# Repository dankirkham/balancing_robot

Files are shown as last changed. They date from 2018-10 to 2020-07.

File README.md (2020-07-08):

# Balancing Robot
A balancing robot that uses a PID control loop with accelerometer feedback to drive stepper motors.

## Mark 1

### Bill of Materials

#### Purchased Parts
- 2 x NEMA 17 Stepper
- 1 x Arduino Uno  
- 2 x Adafruit TB6612 1.2A DC/Stepper Motor Driver Breakout Board
- 1 x Adafruit Triple-Axis Accelerometer - ±2/4/8g @ 14-bit - MMA8451
- 1 x Protoboard
- 1 x 3S 11.1 V 1300 mAh LiPo Battery with XT-60 Connector
- 1 x XT-60 Male Connector
- Hookup Wire
- 3M Dual Lock to hold battery

#### 3D Printed Parts
- 1 x Chassis
- 1 x Circuit Mount
- 2 x Wheels

### Lessons Learned
#### Robot Center-of-Gravity
The center of gravity of the robot is too low. It can be balanced when the motors are unpowered. The robot should have been more top-heavy so that steady-state balance is much more difficult.

#### Reliance on Accelerometer
The robot relies on an accelerometer as its sole instrument for which to measure tilt angle. There are two major issues with this.

1. The stepper motors vibrate violently enough to rattle the accelerometer. When this happens, the accelerometer sees random accelerations greater than 1g. This causes angle measurements to become unreliable. However, if a low-pass filter is applied to the measurement data, this problem seems to go away. When determining a cutoff frequency for the filter, there is a trade-off between vibration noise and the disturbance response of the robot. If the cutoff frequency is too low, the robot will not right it self quickly enough when it is bumped.

2. The angle measurement is not reliable when the robot is under a translational acceleration. If the robot accelerates forward while it is not tilted, the control loop will think its tilted and try to compensate.

A future robot should make use of a gyroscope in addition to the accelerometer. A gyroscope measures rate of change of angle, so it must be integrated over time. This results in angle measurements with more instantaneous accuracy, however the gyroscope will drift over time and must be corrected by the accelerometer.

#### Traction Issues
The robot slipped on smooth surfaces. It seemed to work best on carpet. Future designs should have wheels that provide much better traction.

#### Step Angle
The stepper motors moved 1.8° per step. This resulted in very discrete movements from the robot. The wheels could be seen moving like the second-hand on a quartz clock. A future design might make use of a microstepping driver to make wheel movement more continuous.

## Mark 2

### Bill of Materials

#### Purchased Parts
- 2 x NEMA 17 Stepper
- 1 x Arduino Uno  
- 2 x Adafruit Motor Shield V2
- 1 x Adafruit 9-DOF Accel/Mag/Gyro+Temp Breakout Board - LSM9DS1
- 1 x 3S 11.1 V 1300 mAh LiPo Battery with XT-60 Connector
- 1 x XT-60 Male Connector
- Hookup Wire
- 3M Dual Lock to hold battery
- 2 x RC car tires ([amazon](https://www.amazon.com/gp/product/B0195WYZKE/))

#### 3D Printed Parts
- 1 x Chassis
- 1 x Circuit Mount
- 2 x Wheels
- 1 x Support Bracket

### Improvements Over Mark 1

#### Taller Robot
The robot is now taller and more top heavy. The old robot could sometimes balance by itself with no motor input. This version should be much less stable and require more active control input.

#### Sensors
In addition to an accelerometer, this version uses a gyroscope. The gyroscope provides angular rate data which is integrated over time to provide positional feedback to the control loop.

The sensor has been moved to be on the same axis of rotation as the wheels. I noticed that with the previous version the robot behaved differently when tilted to one side than the other. This is likely because the sensor was not mounted above/below the center of mass. I expect the sensor to perform best when mounted both under the center of mass and on the axis of rotation.

The sensor is now has some vibration damping. This should improve the accelerometer noise that was a problem on the previous robot. I opted to use double-sided foam because it was easy. I may go down the rabbit hole and experiment with other isolation/damping methods in the future.

#### Filtering
In order to combine the accelerometer data and the gyroscope data, this robot makes use of a Kalman filter. This is a statistical filter that models the dynamics of the robot to predict its state. It then uses the measurement data to correct the prediction. By taking into account the noise of the system and the measurements, it provides a very reliable prediction of the tilt angle of the robot.

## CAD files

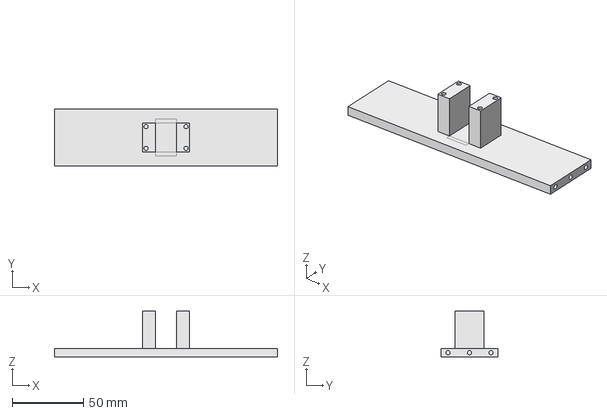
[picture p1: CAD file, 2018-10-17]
mark2/cad/sensor_bracket.FCStd
156.0 x 40.0 x 32.1 mm

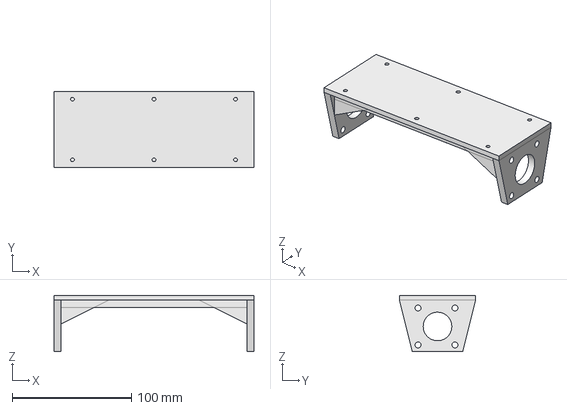
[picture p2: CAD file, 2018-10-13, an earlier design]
mark1/cad/frame.FCStd
168.0 x 64.0 x 47.3 mm

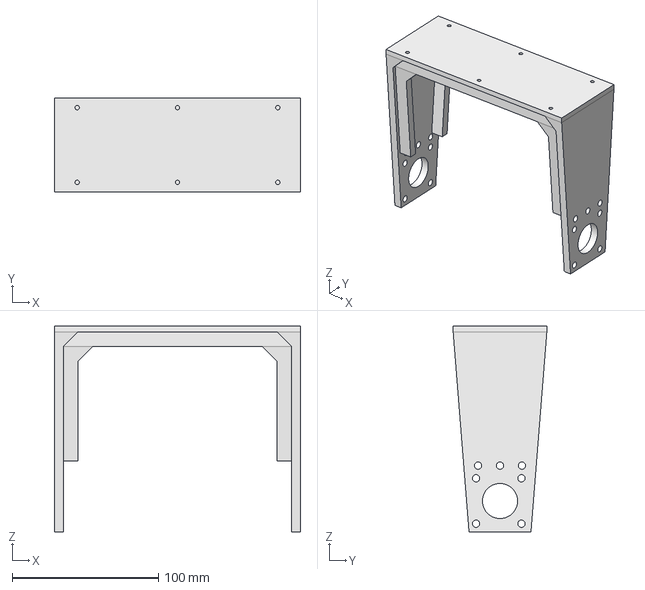
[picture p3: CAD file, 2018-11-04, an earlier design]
mark2/cad/frame.FCStd
168.0 x 64.0 x 140.7 mm

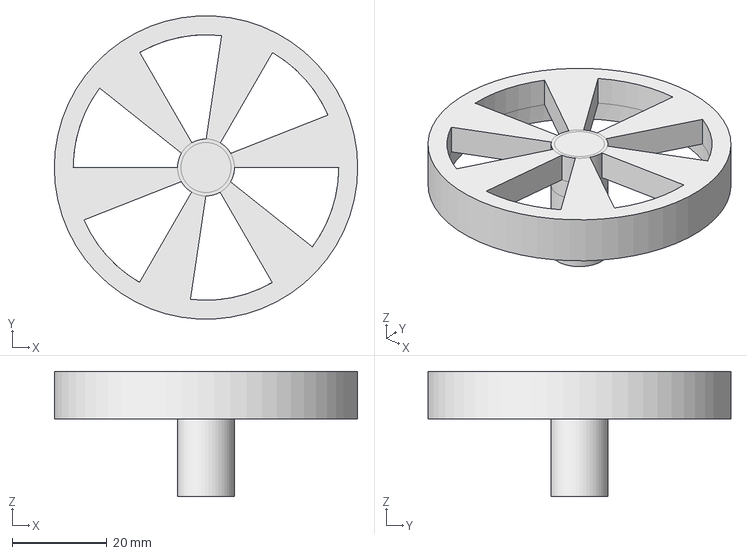
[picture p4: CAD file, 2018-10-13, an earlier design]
mark1/cad/wheel.FCStd
64.0 x 63.9 x 26.4 mm

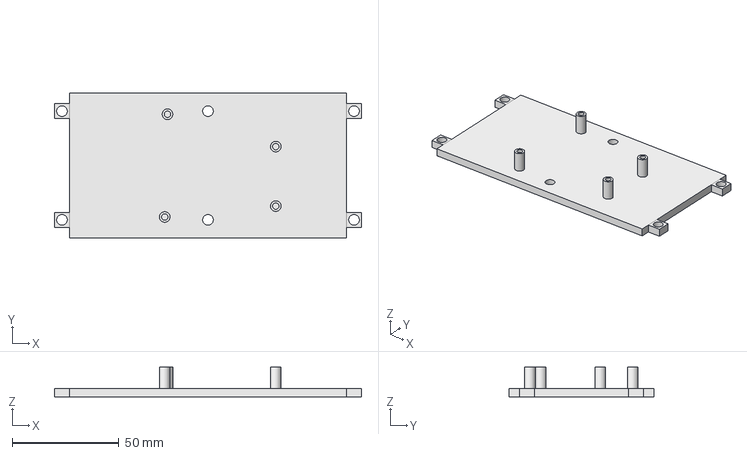
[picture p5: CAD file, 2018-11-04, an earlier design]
mark2/cad/circuit_mount.FCStd
144.0 x 68.0 x 14.0 mm

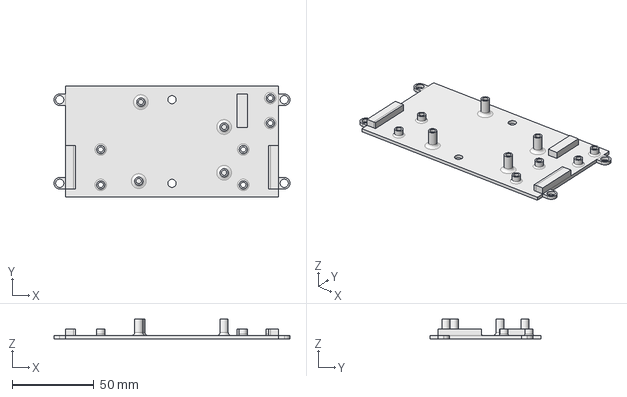
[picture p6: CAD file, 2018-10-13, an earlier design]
mark1/cad/circuit_mount.FCStd
144.0 x 68.0 x 12.0 mm

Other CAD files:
mark1/cad/circuit_mount.stl
mark1/cad/frame.stl
mark1/cad/wheel.stl
mark2/cad/circuit_mount.stl
mark2/cad/frame.stl
mark2/cad/sensor_bracket.stl

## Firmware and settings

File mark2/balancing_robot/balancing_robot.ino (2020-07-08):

#include <Adafruit_MotorShield.h>
#include <Adafruit_LSM9DS1.h>
#include <Adafruit_Sensor.h>
#include <math.h>

#define BATTERY_PIN A2
// 11 Volts
// 509 counts
// 2.494 V at ADC

// 12 Volts
// 556 Counts
// 2.721

const double P = 13;
const double I = 4;
const double D = 40;

const double FILTER_CUTOFF_HERTZ = 1;
const double FILTER_RC = 1 / (2 * M_PI * FILTER_CUTOFF_HERTZ);
const double SET_POINT = 0;
const int STEPS_PER_REVOLUTION = 200;
const double MICROSECONDS_PER_SECOND = 1000000.0;
const double SECONDS_PER_MINUTE = 60.0;
const double MAX_PV = 400.0; // in degrees per seconds
const double DIAGNOSTICS_HERTZ = 5.0;
const double DPS_PER_RPM = 6;
const double GYRO_GAIN = 24;
const double MOVE_THRESHOLD = 5;
const double INTEGRAL_MAX = 10;

const int BATTERY_CELLS = 3;
const double MIN_CELL_VOLTAGE = 3.5;
const double BATTERY_SLOPE = 0.0212766;
const double BATTERY_INTERCEPT = 0.1702;

Adafruit_LSM9DS1 imu;

Adafruit_MotorShield afms = Adafruit_MotorShield();
Adafruit_StepperMotor *left_stepper = afms.getStepper(STEPS_PER_REVOLUTION, 1);
Adafruit_StepperMotor *right_stepper = afms.getStepper(STEPS_PER_REVOLUTION, 2);

double integral = 0;
double last_error = 0;
double last_accelerometer_angle = 0;
double gyro_accumulator = 0;
long last_time;
long last_diagnostics_time;
double steps = 0;
int runs = 0;
boolean motors_stopped = false;

void setup() { 
  Serial.begin(115200);

  imu = Adafruit_LSM9DS1();

  Serial.println("Starting IMU");
  if (!imu.begin()) {
    Serial.println("IMU could not be started.");
    while(1);
  }
  Serial.println("IMU Started");

  imu.setupAccel(imu.LSM9DS1_ACCELRANGE_2G);
  imu.setupMag(imu.LSM9DS1_MAGGAIN_4GAUSS);
  imu.setupGyro(imu.LSM9DS1_GYROSCALE_245DPS);

  left_stepper->setSpeed(120);
  right_stepper->setSpeed(120);

  // TODO: Send configuration to host

  last_time = micros();

  afms.begin();

  // Change the i2c clock to 400KHz, this speeds up motor control
  TWBR = ((F_CPU /400000l) - 16) / 2; 
}

void loop() {
  // Find time delta
  long current_time = micros();
  double delta = double(current_time - last_time) / MICROSECONDS_PER_SECOND;
  last_time = current_time;
  runs += 1;

  // Compute battery voltage
  double voltage = analogRead(BATTERY_PIN) * BATTERY_SLOPE + BATTERY_INTERCEPT;
  double cell_voltage = voltage / BATTERY_CELLS;

  if (!motors_stopped && cell_voltage < MIN_CELL_VOLTAGE) {
    motors_stopped = true;
  }

  // Find Error
  sensors_event_t accel, mag, gyro, temp;
  imu.getEvent(&accel, &mag, &gyro, &temp);

  // Accelerometer Angle
  double x = accel.acceleration.x;
  double z = accel.acceleration.z;
  // Simple infinite impulse response filter
  double alpha = delta / (FILTER_RC + delta);
  double raw_accelerometer_angle = SET_POINT - (atan2(-x, -z) * 180 / M_PI);
  double accelerometer_angle = (alpha * raw_accelerometer_angle) + (1 - alpha) * last_accelerometer_angle;
  last_accelerometer_angle = raw_accelerometer_angle;

  // Gyroscope Angle
  gyro_accumulator -= gyro.gyro.y * delta * GYRO_GAIN;
  double error = gyro_accumulator * 0.9 + accelerometer_angle * 0.1;
  gyro_accumulator = error;
//  double error = gyro_accumulator;

  // Find integral and derivative
  integral = integral + (error * delta);
  double derivative = error - last_error;
  // Integral reset
//  if (
//    error < 0 && last_error > 0 ||
//    error > 0 && last_error < 0
//  ) {
//    integral = 0;
//  }
  // Integral cap
//  if (integral > INTEGRAL_MAX) {
//    integral = INTEGRAL_MAX;
//  } else if (integral < -INTEGRAL_MAX) {
//    integral = -INTEGRAL_MAX;
//  }
  last_error = error;

  // Calculate Process Value with gains. Process Value is velocity!
  double p = P * error;
  double i = I * integral;
  double d = D * derivative;
  double process_value = p + i + d;
  // Cap PV
  if (process_value > MAX_PV) {
    process_value = MAX_PV;
  } else if (process_value < -MAX_PV) {
    process_value = -MAX_PV;
  }

  // Find out how many steps need to be taken for this time slice
  steps = steps + (process_value * STEPS_PER_REVOLUTION / SECONDS_PER_MINUTE * delta);

  // Seperate fractional from integral part.
  // Fractional part is rolled over to next iteration.
  double steps_to_take_right_now;
  steps = modf(steps, &steps_to_take_right_now);

  // Diagnostics
  if ((double(current_time - last_diagnostics_time) / MICROSECONDS_PER_SECOND) > (1 / DIAGNOSTICS_HERTZ)) {
    last_diagnostics_time = current_time;
//    Serial.print(gyro_accumulator);
//    Serial.print(' ');
//    Serial.print(accelerometer_angle);
//    Serial.print(' ');
    Serial.print(p);
    Serial.print(' ');
    Serial.print(i);
    Serial.print(' ');
    Serial.print(d);
//    Serial.print(' ');
//    Serial.print(steps);
//    Serial.print(' ');
//    Serial.print(steps_to_take_right_now);
    Serial.print(' ');
    Serial.print(process_value);
    Serial.print(' ');
    Serial.print(runs);
    Serial.print(' ');
    Serial.print(cell_voltage);
    if (motors_stopped) {
      Serial.print(" UV FAULT");
    }
    Serial.print('\n');
    runs = 0;
  }

  if (motors_stopped) {
    left_stepper->release();
    right_stepper->release();
    return;
  }

  //   Move the motors
  while (steps_to_take_right_now != 0) {
    if (steps_to_take_right_now >= 32) {
      left_stepper->onestep(BACKWARD, DOUBLE);
      right_stepper->onestep(FORWARD, DOUBLE);
      steps_to_take_right_now -= 32;
    } else if (steps_to_take_right_now >= 16) {
      left_stepper->onestep(BACKWARD, SINGLE);
      right_stepper->onestep(FORWARD, SINGLE);
      steps_to_take_right_now -= 16;
    } else if (steps_to_take_right_now >= 8) {
      left_stepper->onestep(BACKWARD, INTERLEAVE);
      right_stepper->onestep(FORWARD, INTERLEAVE);
      steps_to_take_right_now -= 8;
    } else if (steps_to_take_right_now >= 1) {
      left_stepper->onestep(BACKWARD, MICROSTEP);
      right_stepper->onestep(FORWARD, MICROSTEP);
      steps_to_take_right_now -= 1;
    } else if (steps_to_take_right_now <= -32) {
      left_stepper->onestep(FORWARD, DOUBLE);
      right_stepper->onestep(BACKWARD, DOUBLE);
      steps_to_take_right_now += 32;
    } else if (steps_to_take_right_now <= -16) {
      left_stepper->onestep(FORWARD, SINGLE);
      right_stepper->onestep(BACKWARD, SINGLE);
      steps_to_take_right_now += 16;
    } else if (steps_to_take_right_now <= -8) {
      left_stepper->onestep(FORWARD, INTERLEAVE);
      right_stepper->onestep(BACKWARD, INTERLEAVE);
      steps_to_take_right_now += 8;
    } else if (steps_to_take_right_now <= -1) {
      left_stepper->onestep(FORWARD, MICROSTEP);
      right_stepper->onestep(BACKWARD, MICROSTEP);
      steps_to_take_right_now += 1;
    }
  }
}

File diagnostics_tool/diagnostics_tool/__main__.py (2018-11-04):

from .receiver import Receiver
from multiprocessing import Queue, Pipe
import argparse
import matplotlib.pyplot as plt

def main():
    parser = argparse.ArgumentParser()
    parser.add_argument('port')
    parser.add_argument('--baudrate', type=int, default=115200)
    parser.add_argument('-o', help='output-file')

    args = parser.parse_args()

    queue = Queue()
    signal1, signal2 = Pipe()

    receiver = Receiver(queue, signal1, args.port, baudrate=args.baudrate, outfile=args.o)

    receiver.start()

    fig = plt.figure()
    plt.axis([0, 1000, -90, 90])
    fig.suptitle('Angle Error')
    plt.xlabel('elapsed time (s)')
    plt.ylabel('angle error (°)')

    sample_count = 0
    errors = []

    error_line, = plt.plot(errors, 'k')

    while True:
        message = queue.get()
        print(message)

        errors.append(message['error'])
        sample_count += 1

        error_line.set_xdata(range(sample_count))
        error_line.set_ydata(errors)

        # plt.plot(errors, 'k')

        plt.pause(0.05)

    plt.show()

if __name__ == "__main__":
    main()

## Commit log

2018-10-13 Added CAD files.
    [circuit_mount.FCStd, circuit_mount.stl, frame.FCStd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]
2018-10-15 Experimenting with Kalman filters.
    [upright_no_motors.csv, upright_with_motors.csv]
2018-10-17 Mark 2 CAD started.
    [frame.FCStd, frame.stl, sensor_bracket.FCStd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]
2018-11-04 Removed accelerometer and stepper driver mounts from circuit mount. Made mount thicker.
    [circuit_mount.FCStd, circuit_mount.stl]
2018-11-04 Improved strength of Mark 2 Frame.
    [frame.FCStd, frame.stl]
2018-11-04 Change sensor to Accelerometer/Gyro.
2018-11-04 diagnostics tool can now log to CSV and also logs raw, unfiltered error.
    [__main__.py, receiver.py]
2018-11-04 Updated kalmanf filter code.
2018-11-04 Created Mark 1 directory.
    [circuit_mount.FCStd, circuit_mount.stl, frame.FCStd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]
